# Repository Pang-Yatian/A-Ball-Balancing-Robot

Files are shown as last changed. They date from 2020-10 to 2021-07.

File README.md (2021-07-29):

# A-Ball-Balancing-Robot
## Brief introduction
A ball balancing robot is a kind of dynamical stable robot, which is designed to balance on a ball by itself, while the ball can move in any direction under the control of the robot. Actuation is realized by using DC motors to drive three omnidirectional wheels rotating, making the robot body reach its equilibrium point. An inertial measurement unit is used to detect the change in attitude angles. Based on kinematic analysis, Proportional-Integral-Derivative controllers are implemented to stabilize and control the robot.

video:  https://youtu.be/On0e1YCgcag

https://www.bilibili.com/video/BV1TJ411x7tR?p=3

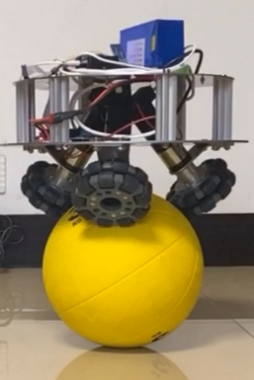
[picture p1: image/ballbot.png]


## Run
The code needs Keil uvison5 IDE to open.

--->dynamical control code\USER\Minibalance.uvprojx

## Hardware composition

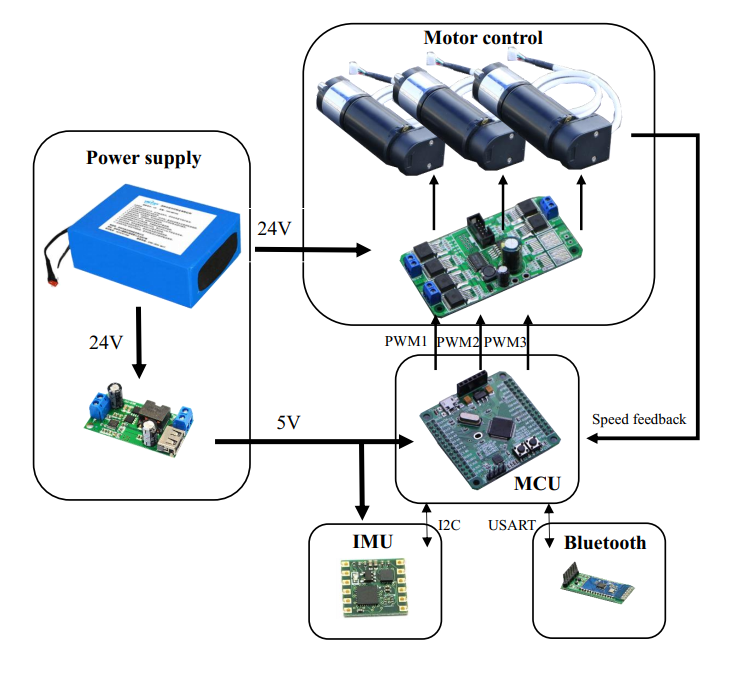
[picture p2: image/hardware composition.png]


## Hardware list

MCU:STM32F103 module

DC motor: MD36NP51 with photoelectric encoder (24V)

Motor driver: BTN7971 module

Omniwheel: diameter 100mm

Battery: 5AH 24V 5000mah

Ball: v1-v2 standard football, final version 3kg medicine ball (225mm)

IMU: MPU-6050 module

## Performance 

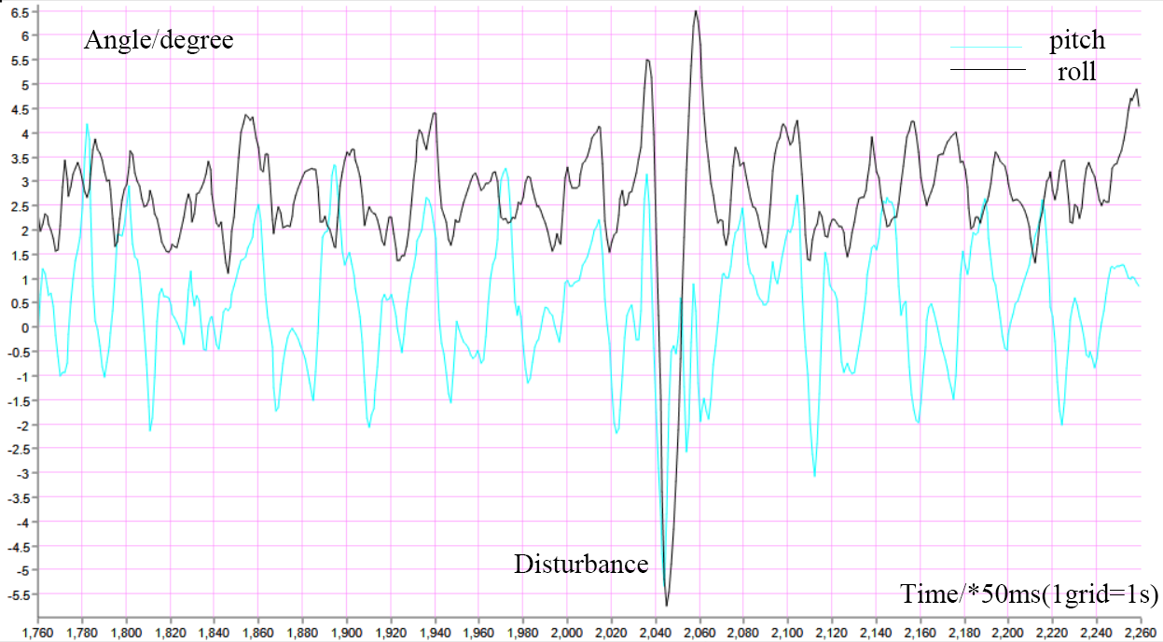
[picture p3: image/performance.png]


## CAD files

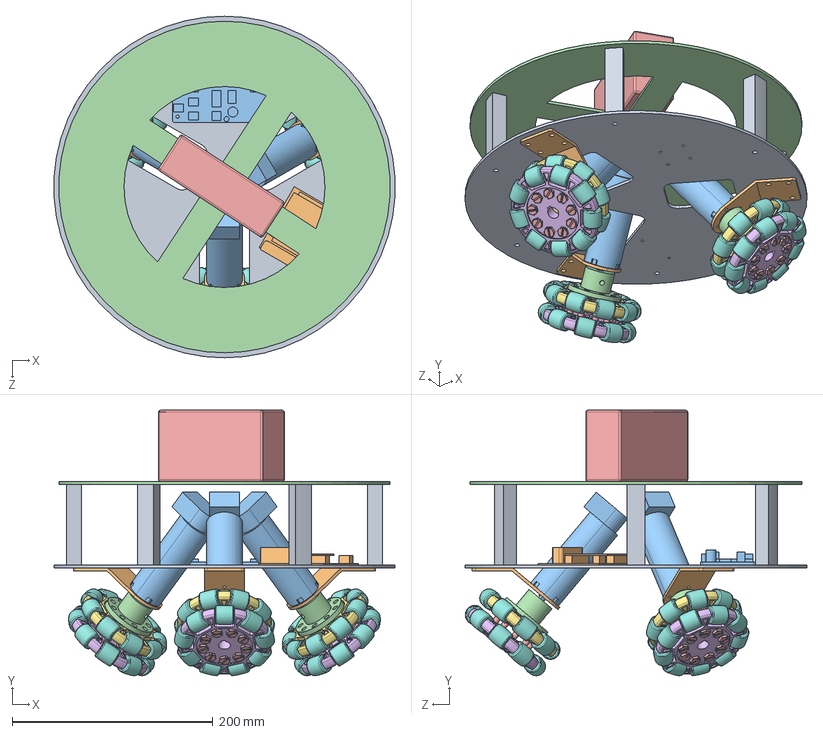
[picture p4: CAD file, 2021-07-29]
Mechanic/ballbot 50度.SLDASM
339.4 x 264.3 x 340.0 mm
底盘
电机支架 x 3
电机.stp x 3
lianzhouqi x 3
hex bolts with slot on head grade ab gb x 27
omnidirectionalwheels x 3
omnidirectionalwheels2 x 3
wheel x 54
支柱 x 6
stm32f103rc
BTN7971
板1
battery

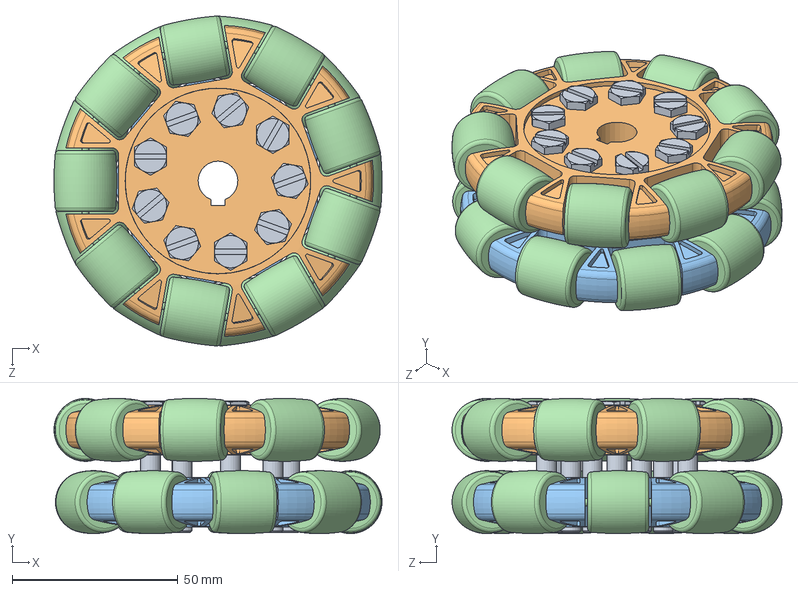
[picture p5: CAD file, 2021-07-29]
Mechanic/parts/omniwheel.SLDASM
99.0 x 40.8 x 99.6 mm
hex bolts with slot on head grade ab gb x 9
omnidirectionalwheels
omnidirectionalwheels2
wheel x 18

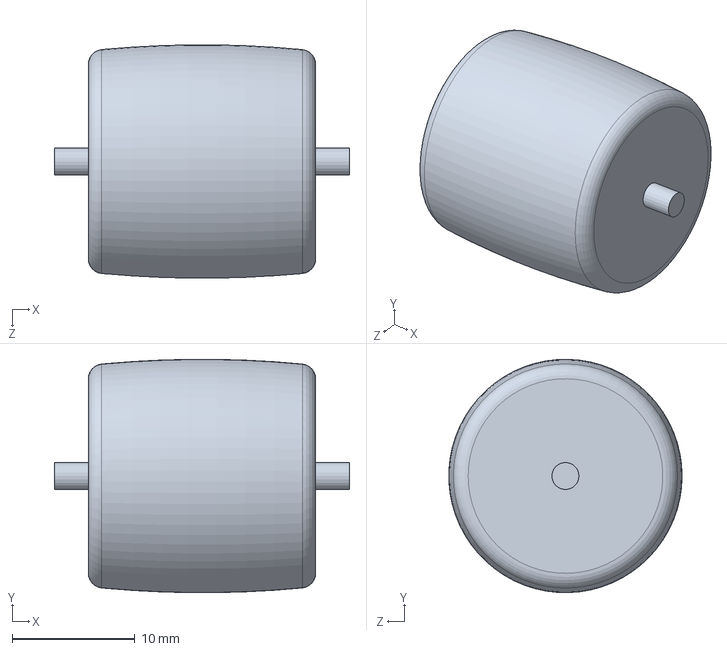
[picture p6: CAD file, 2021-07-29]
Mechanic/parts/part/wheel.SLDPRT
24.0 x 19.0 x 19.0 mm

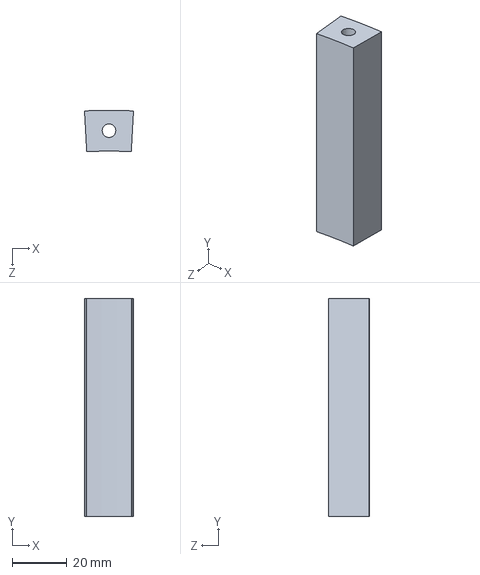
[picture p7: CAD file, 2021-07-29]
Mechanic/parts/支柱.SLDPRT
18.0 x 80.0 x 15.2 mm

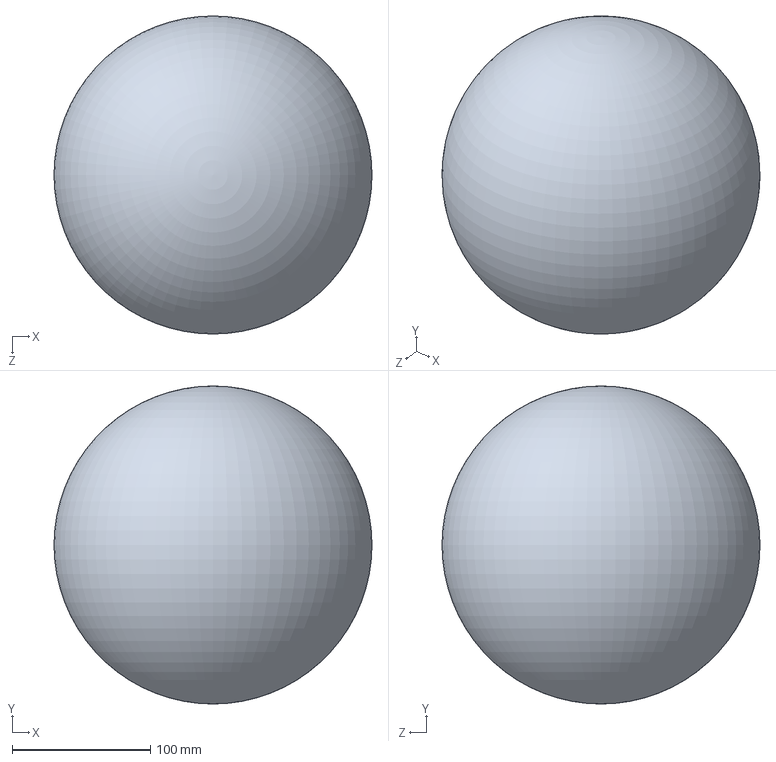
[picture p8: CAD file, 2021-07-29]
Mechanic/parts/ball.SLDPRT
230.0 x 230.0 x 230.0 mm

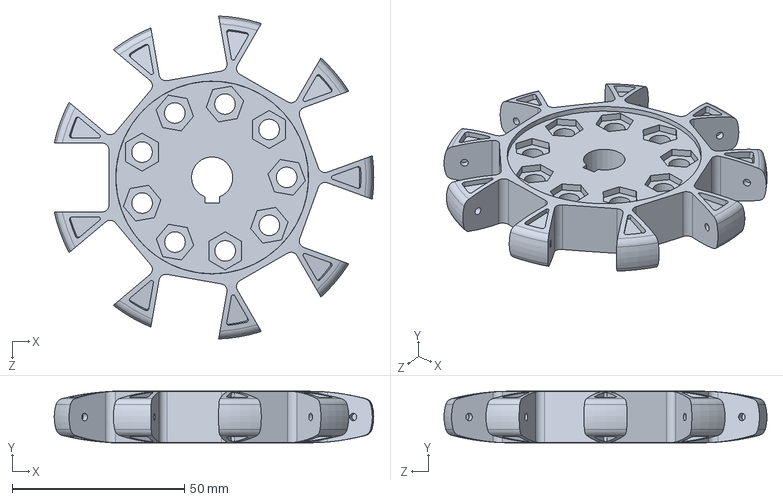
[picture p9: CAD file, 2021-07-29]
Mechanic/parts/part/omnidirectionalwheels.SLDPRT
92.9 x 15.0 x 93.9 mm

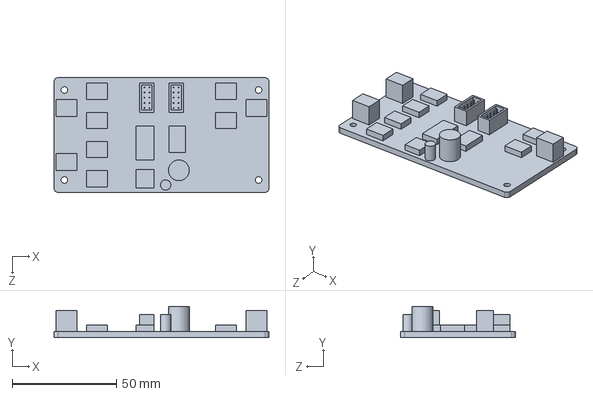
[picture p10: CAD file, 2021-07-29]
Mechanic/parts/BTN7971.SLDPRT
103.2 x 15.0 x 55.2 mm

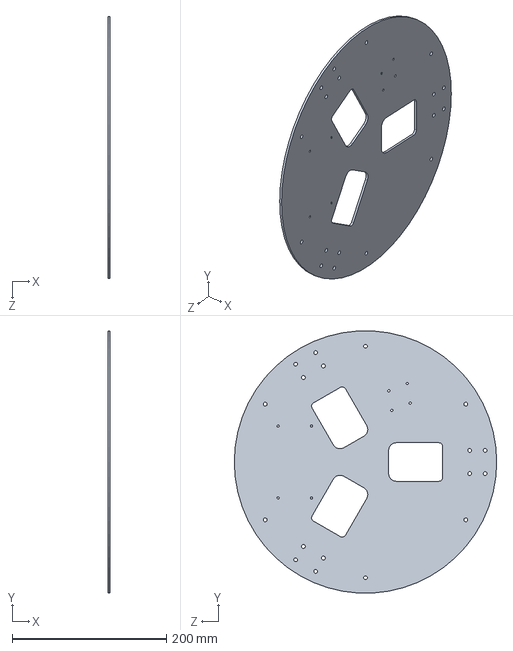
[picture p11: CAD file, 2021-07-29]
Mechanic/parts/底盘.SLDPRT
3.00 x 339.4 x 340.0 mm

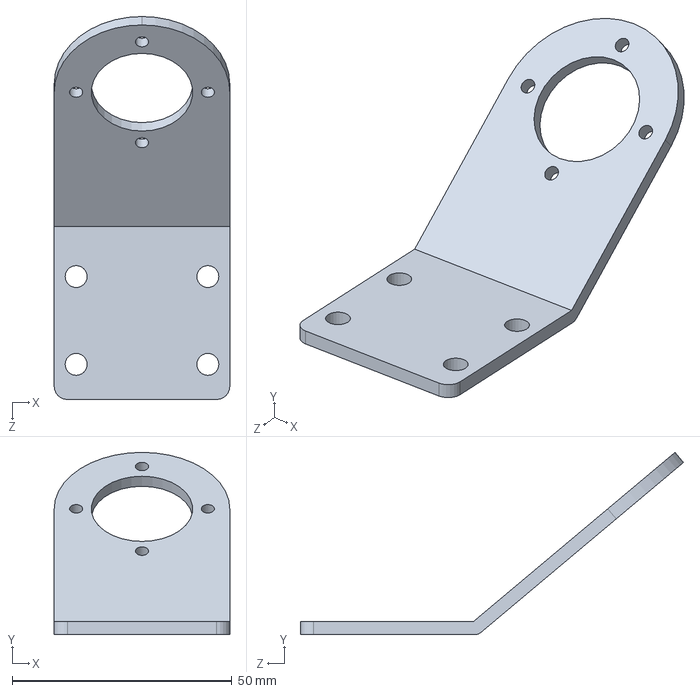
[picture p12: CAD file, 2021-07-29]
Mechanic/parts/电机支架.SLDPRT
40.0 x 41.5 x 87.2 mm

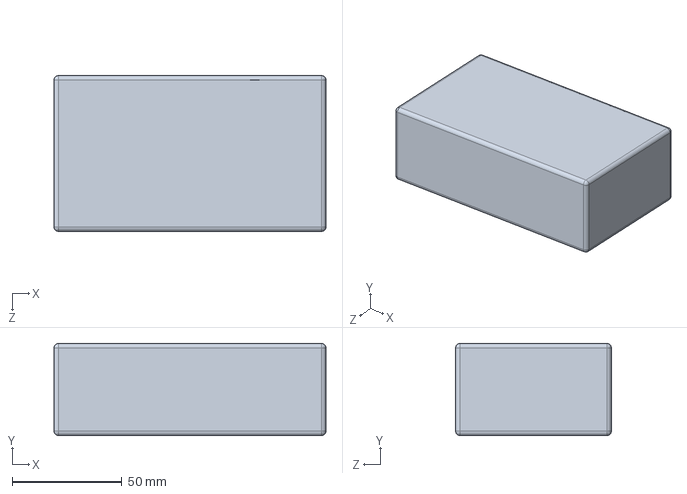
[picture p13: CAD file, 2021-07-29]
Mechanic/parts/battery.SLDPRT
124.0 x 42.0 x 71.0 mm

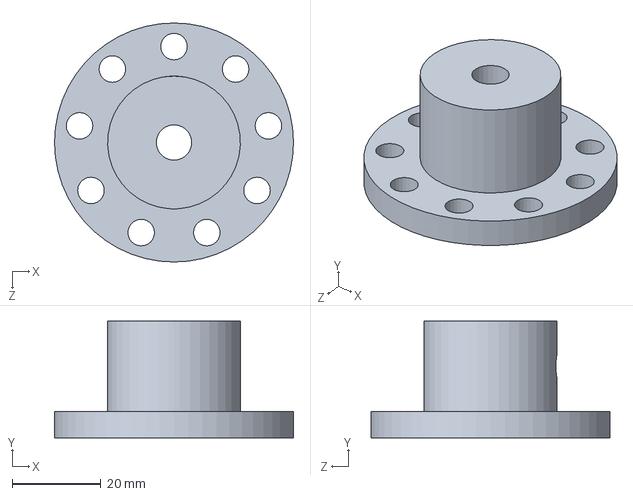
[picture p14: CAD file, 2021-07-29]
Mechanic/parts/lianzhouqi.SLDPRT
54.0 x 26.4 x 54.0 mm

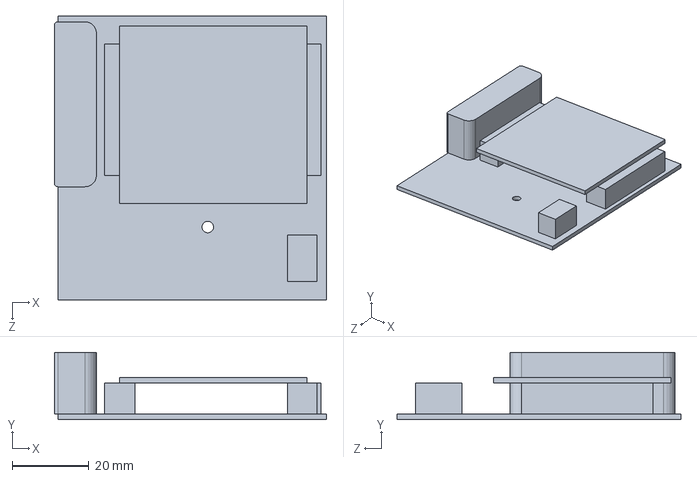
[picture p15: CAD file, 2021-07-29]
Mechanic/parts/stm32f103rc.SLDPRT
71.0 x 17.5 x 74.0 mm

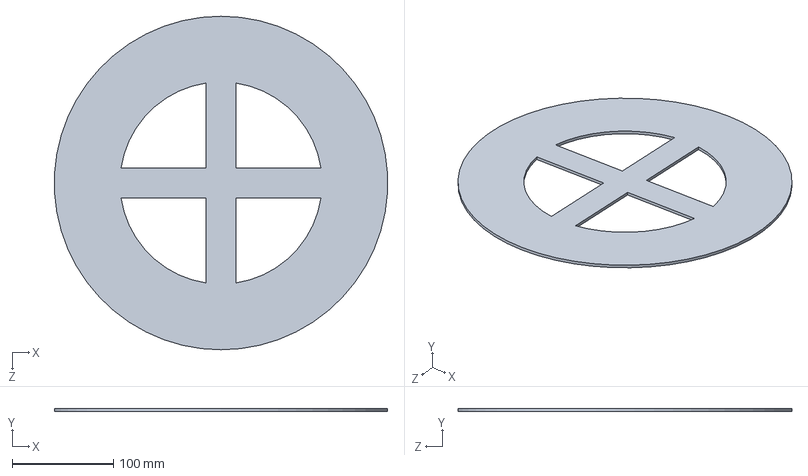
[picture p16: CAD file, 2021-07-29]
Mechanic/parts/板1.SLDPRT
329.4 x 3.00 x 330.0 mm

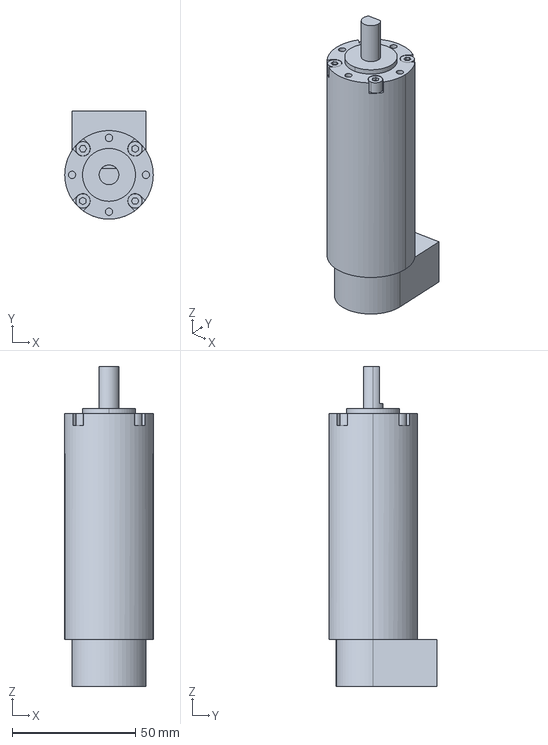
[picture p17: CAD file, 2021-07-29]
Mechanic/parts/电机.stp
36.0 x 44.0 x 130.0 mm

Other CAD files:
Mechanic/parts/part/omnidirectionalwheels2.SLDPRT

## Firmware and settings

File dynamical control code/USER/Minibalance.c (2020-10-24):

#include "sys.h"
  /**************************************************************************
作者：Pang Yatian
*
**************************************************************************/ 
u8 Flag_Stop=1,Flag_Show,Flag_Zero;      //停止标志位和 显示标志位 默认停止 显示打开
int Encoder_A,Encoder_B,Encoder_C;          //编码器的脉冲计数
u8 Flag_Qian,Flag_Hou,Flag_Left,Flag_Right,Turn_Left,Turn_Right;                  
long int Motor_A,Motor_B,Motor_C;        //电机PWM变量
long int Target_A,Target_B,Target_C;     //电机目标值
float Encoder_X,Encoder_Y,Encoder_Z,Position_X,Position_Y;;
int Voltage;                             //电池电压采样相关的变量                       
u8 delay_50,delay_flag,sudu=1;                          //延时相关变量
u8 Turn_Flag,PID_Send;  //CAN和串口控制相关变量
float Angle_Balance_X,Angle_Balance_Y,Angle_Balance_Z,Gyro_Balance_X,Gyro_Balance_Z,Gyro_Balance_Y,Move_X,Move_Y,Move_Z;   //三轴角度和XYZ轴目标速度
float	Balance_Kp=255,Balance_Kd=120,Balance_Kp1=265,Balance_Kd1=120,Velocity_Kp=78,Velocity_Ki=50,Velocity_Kp1=123,Velocity_Ki1=60,Turn_Kp=25,Turn_Kd=87;  //控制PID参数 151 88
int Angle_Zero_X, Angle_Zero_Y,Angle_Bias_X, Angle_Bias_Y;
int main(void)
{ 
	Stm32_Clock_Init(9);            //=====系统时钟设置
	delay_init(72);                 //=====延时初始化
	JTAG_Set(JTAG_SWD_DISABLE);     //=====关闭JTAG接口
	JTAG_Set(SWD_ENABLE);           //=====打开SWD接口 可以利用主板的SWD接口调试
	LED_Init();                     //=====初始化与 LED 连接的硬件接口
	KEY_Init();                     //=====按键初始化
	OLED_Init();                    //=====OLED初始化
	uart_init(72,128000);           //=====串口1初始化
	uart2_init(36,9600);            //=====串口2初始化
 // uart3_init(36,115200);          //=====串口3初始化 
	Encoder_Init_TIM2();            //=====编码器接口
	Encoder_Init_TIM3();            //=====编码器接口
	Encoder_Init_TIM4();            //=====初始化编码器C
	Encoder_Init_TIM5();            //=====初始化编码器D
	Adc_Init();                     //=====adc初始化
	IIC_Init();                     //=====IIC初始化
  MPU6050_initialize();           //=====MPU6050初始化	
  DMP_Init();                     //=====初始化DMP     
	MiniBalance_PWM_Init(7199,0);   //=====初始化PWM 10KHZ，用于驱动电机
  EXTI_Init();                    //=====MPU6050 5ms定时中断初始化
	while(1)
		{		
	    if(Flag_Show==0)           //使用MiniBalance APP和OLED显示屏
			{
				APP_Show();	              
				oled_show();             //===显示屏打开
	    }
    	else                       //使用MiniBalance上位机 上位机使用的时候需要严格的时序，故此时关闭app监控部分和OLED显示屏
  		{
				DataScope();              //开启MiniBalance上位机
			}
			delay_flag=1;	
			delay_50=0;
			while(delay_flag);	       //通过MPU6050的INT中断实现的50ms精准延时				
		} 
}

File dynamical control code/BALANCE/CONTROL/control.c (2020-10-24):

#include "control.h"	
#include "filter.h"	
  /**************************************************************************
作者：Pang Yatian
*
**************************************************************************/

u8 Flag_Target,Flag_Target2,Flag_Change;                             //相关标志位
u8 temp1;                                               //临时变量
float Voltage_Count,Voltage_All; 											 //电压采样相关变量
int Balance_Pwm_X,Velocity_Pwm_X,Balance_Pwm_Y,Velocity_Pwm_Y,Balance_Pwm_Z;
#define X_PARAMETER          (0.5f)               
#define Y_PARAMETER           (sqrt(3)/2.f)      
#define L_PARAMETER            (1.0f)    
/**************************************************************************
函数功能：小车运动数学模型
入口参数：X Y Z 三轴速度或者位置
返回  值：无
**************************************************************************/
void Kinematic_Analysis(float Vx,float Vy,float Vz)
{
	      Target_A   = -Vx + L_PARAMETER*Vz;
        Target_B   = X_PARAMETER*Vx - Y_PARAMETER*Vy + L_PARAMETER*Vz;
	      Target_C   = X_PARAMETER*Vx + Y_PARAMETER*Vy + L_PARAMETER*Vz;
}
/**************************************************************************
函数功能：小车运动 正运动学分析 注：实际注释掉的是理想的运动学分析，实际使用放大了3倍，对计算结果没影响，主要是避免舍去误差
入口参数：A B C三个电机的速度
返回  值：无
**************************************************************************/
void Encoder_Analysis(float Va,float Vb,float Vc)
{
		Encoder_X=Va*2-Vb-Vc;
		Encoder_Y=(Vc-Vb)*sqrt(3);
		Encoder_Z=Va+Vb+Vc;
}
/**************************************************************************
函数功能：所有的控制代码都在这里面
         5ms定时中断由MPU6050的INT引脚触发
         严格保证采样和数据处理的时间同步				 
**************************************************************************/
int EXTI15_10_IRQHandler(void) 
{    
	 if(INT==0)		
	{     
		  EXTI->PR=1<<15;                                                      //清除LINE5上的中断标志位  	        		
		  if(delay_flag==1)
			 {
				 if(++delay_50==10)	 delay_50=0,delay_flag=0;                     //给主函数提供50ms的精准延时
			 }             
       Flag_Target2=!Flag_Target2;  //角度采集分频标志位
			 if(Flag_Target2==1)
			 {
			 	Read_DMP();  //采集角度
				Key();//扫描按键变化	
		    if(Flag_Show==0)Led_Flash(100);  //===LED闪烁;常规模式 1s改变一次指示灯的状态	
				else Led_Flash(0); //上位机模式常亮
				Voltage_All+=Get_battery_volt();   //多次采样累积采集电池电压
			  if(++Voltage_Count==100) Voltage=Voltage_All/100,Voltage_All=0,Voltage_Count=0;//求平均值 获取电池电压	 
         return 0;				 
			 }
			Encoder_A=-Read_Encoder(2);  //===读取编码器的值 为了保证M法测速的时间基准，首先读取编码器数据
			Encoder_B=-Read_Encoder(3);  //===读取编码器的值  
			Encoder_C=-Read_Encoder(4);  //===读取编码器的值+=Encoder_A/20;
				
			Angle_Bias_X =Angle_Balance_X-Angle_Zero_X;		//获取Y方向的偏差
		  Angle_Bias_Y =Angle_Balance_Y-Angle_Zero_Y;		//获取Y方向的偏差
			Encoder_Analysis(Encoder_A,Encoder_B,Encoder_C);//对编码器的数据进行正运动学分析
			  Position_X+=Encoder_X;
			  Position_Y+=Encoder_Y;
	  	Read_DMP();   //读取角度 
			Balance_Pwm_X= balance_X(Angle_Bias_X,Gyro_Balance_X);//X方向的倾角控制
			Balance_Pwm_Y= balance_Y(Angle_Bias_Y,Gyro_Balance_Y);	//Y方向的倾角控制
			Balance_Pwm_Z= -balance_Z(Encoder_Z,Gyro_Balance_Z);		//Z方向倾角控制
       if(++Flag_Target==4)			//速度控制分频标志位 
			  {
				Velocity_Pwm_X=velocity_X(Encoder_X);  //X方向的速度控制  
				Velocity_Pwm_Y=velocity_Y(Encoder_Y);  //Y方向的速度控制
					Flag_Target=0;				 
			  }
			  Move_X =Balance_Pwm_X+Velocity_Pwm_X;   //===X方向控制量累加					
			  Move_Y =Balance_Pwm_Y+Velocity_Pwm_Y;   //===Y方向控制量累加					
			  Move_Z=Balance_Pwm_Z;				 //===Z方向控制量累加	
 				Kinematic_Analysis(Move_X,Move_Y,Move_Z);//逆运动学分析，得到A B C电机控制量
			  Xianfu_Pwm(3000);//===PWM频率限幅
				Motor_A=Target_A;//直接调节PWM占空比 
				Motor_B=Target_B;//直接调节PWM占空比
				Motor_C=Target_C;//直接调节PWM占空比
		    if(Turn_Off(Voltage)==0)  //===如果电池电压不存在异常
				Set_Pwm(Motor_A,Motor_B,Motor_C);    //赋值给PWM寄存器	
					 if(Flag_Zero)  // //这是人为更新零点值
				 {
						 Angle_Zero_Y=Angle_Balance_Y;//Y方向角度更新
						 Angle_Zero_X=Angle_Balance_X;//X方向角度更新
						 Flag_Zero=0;//清零过程仅执行一次 等待下一次指令
				 }		 				 
 }
	 return 0;			
} 
/**************************************************************************
函数功能：Z轴控制
入口参数：Z轴速度、Z轴角速度
返回  值：Z轴控制控制PWM
作    者：Pang Yatian
**************************************************************************/
int balance_Z(float Velocity,float Gyro)
{  
   float Bias,Target;   //偏差和目标值
	 static float Target_Velocity=600;//遥控的速度
	 int balance,turn_kd;
	 if(Turn_Left==1)Target=Target_Velocity/sudu,turn_kd=0;   //控制自转
	 else if(Turn_Right==1)Target=-Target_Velocity/sudu,turn_kd=0;
	 else Target=0,turn_kd=Turn_Kd;
	 Bias=Velocity-Target;        //===求出平衡的角度中值 和机械相关
	 balance=Turn_Kp*Bias/10+Gyro*turn_kd/100;   //===计算平衡控制的电机PWM  PD控制   kp是P系数 kd是D系数  
	 return balance;
}
/**************************************************************************
函数功能：直立PD控制Y
入口参数：角度、角速度
返回  值：直立控制PWM
作    者：Pang Yatian
**************************************************************************/
int balance_Y(float Angle,float Gyro)
{  
   float Bias;
	 int balance;
	 Bias=Angle;        //===求出平衡的角度中值 和机械相关
	 balance=Balance_Kp1*Bias+Gyro*Balance_Kd1/100;   //===计算平衡控制的电机PWM  PD控制   kp是P系数 kd是D系数 
	 return balance;
}
/**************************************************************************
函数功能：直立PD控制
入口参数：角度、角速度
返回  值：直立控制PWM
作    者：Pang Yatian
**************************************************************************/
int balance_X(float Angle,float Gyro)
{  
   float Bias;
	 int balance;
	 Bias=Angle;        //===求出平衡的角度中值 和机械相关
	 balance=Balance_Kp*Bias+Gyro*Balance_Kd/100;   //===计算平衡控制的电机PWM  PD控制   kp是P系数 kd是D系数 
	 return balance;
}

/**************************************************************************
函数功能：速度PI控制 修改前进后退速度，请修Target_Velocity
入口参数：左轮速度、右轮速度
返回  值：速度控制PWM
作    者：Pang Yatian
**************************************************************************/
int velocity_X(int velocity)
{  
    static float Velocity,Encoder_Least,Encoder,Movement;
	  static float Target_Velocity=1200;//遥控的速度
	  static float Encoder_Integral;  //积分变量
			if(1==Flag_Left)    	Movement=Target_Velocity/sudu;	           //===前进标志位置1 
		else if(1==Flag_Right)	Movement=-Target_Velocity/sudu;           //===后退标志位置1
  	else  Movement=0;
//   //=============速度PI控制器=======================//	
		Encoder_Least=velocity;          //速度采集  
		Encoder *= 0.7;		                                                //===一阶低通滤波器       
		Encoder += Encoder_Least*0.3;	                                    //===一阶低通滤波器    
		Encoder_Integral +=Encoder;                                       //===积分出位移 
		Encoder_Integral +=Movement;                                      //===接收遥控器数据，控制前进后退
		if(Encoder_Integral>550000)  	Encoder_Integral=550000;             //===积分限幅
		if(Encoder_Integral<-550000)	Encoder_Integral=-550000;              //===积分限幅	
	  Velocity=Encoder*Velocity_Kp/100+Encoder_Integral*Velocity_Ki/5000;        //===速度控制	
  	if(Flag_Stop)   Encoder_Integral=0,Encoder=0;      //===电机关闭后清除积分
	  return Velocity;
}
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

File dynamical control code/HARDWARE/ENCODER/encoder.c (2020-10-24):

#include "encoder.h"
  /**************************************************************************
作者：Pang Yatian
*
**************************************************************************/
/**************************************************************************
函数功能：把TIM2初始化为编码器接口模式
入口参数：无
返回  值：无
**************************************************************************/
void Encoder_Init_TIM2(void)
{
//	RCC->APB2ENR|=1<<0;    //开启辅助时钟
	AFIO->MAPR|=1<<8;      //01部分重映射
	RCC->APB1ENR|=1<<0;     //TIM2时钟使能
	RCC->APB2ENR|=1<<2;    //使能PORTA时钟
	RCC->APB2ENR|=1<<3;    //使能PORTB时钟
	GPIOA->CRH&=0X0FFFFFFF;//PA15
	GPIOA->CRH|=0X40000000;//浮空输入
	
	GPIOB->CRL&=0XFFFF0FFF;//PB3
	GPIOB->CRL|=0X00004000;//浮空输入
	TIM2->DIER|=1<<0;   //允许更新中断				
	TIM2->DIER|=1<<6;   //允许触发中断
	MY_NVIC_Init(1,3,TIM2_IRQn,1);
	TIM2->PSC = 0x0;//预分频器
	TIM2->ARR = ENCODER_TIM_PERIOD;//设定计数器自动重装值 
	TIM2->CR1 &=~(3<<8);// 选择时钟分频：不分频
	TIM2->CR1 &=~(3<<5);// 选择计数模式:边沿对齐模式
		
	TIM2->CCMR1 |= 1<<0; //CC1S='01' IC1FP1映射到TI1
	TIM2->CCMR1 |= 1<<8; //CC2S='01' IC2FP2映射到TI2
	TIM2->CCER &= ~(1<<1);	 //CC1P='0'	 IC1FP1不反相，IC1FP1=TI1
	TIM2->CCER &= ~(1<<5);	 //CC2P='0'	 IC2FP2不反相，IC2FP2=TI2
//	TIM2->CCMR1 |= 3<<4; //	IC1F='1000' 输入捕获1滤波器
	TIM2->SMCR |= 3<<0;	 //SMS='011' 所有的输入均在上升沿和下降沿有效
	TIM2->CR1 |= 0x01;    //CEN=1，使能定时器
}
/**************************************************************************
函数功能：把TIM3初始化为编码器接口模式
入口参数：无
返回  值：无
**************************************************************************/
void Encoder_Init_TIM3(void)
{
	RCC->APB1ENR|=1<<1;     //TIM2时钟使能
	RCC->APB2ENR|=1<<3;    //使能PORTA时钟
	GPIOA->CRL&=0X00FFFFFF;//PA6 PA7
	GPIOA->CRL|=0X44000000;//浮空输入
	TIM3->DIER|=1<<0;   //允许更新中断				
	TIM3->DIER|=1<<6;   //允许触发中断
	MY_NVIC_Init(1,3,TIM3_IRQn,1);
	TIM3->PSC = 0x0;//预分频器
	TIM3->ARR = ENCODER_TIM_PERIOD;//设定计数器自动重装值 
	TIM3->CR1 &=~(3<<8);// 选择时钟分频：不分频
	TIM3->CR1 &=~(3<<5);// 选择计数模式:边沿对齐模式
		
	TIM3->CCMR1 |= 1<<0; //CC1S='01' IC1FP1映射到TI1
	TIM3->CCMR1 |= 1<<8; //CC2S='01' IC2FP2映射到TI2
	TIM3->CCER &= ~(1<<1);	 //CC1P='0'	 IC1FP1不反相，IC1FP1=TI1
	TIM3->CCER &= ~(1<<5);	 //CC2P='0'	 IC2FP2不反相，IC2FP2=TI2
//	TIM2->CCMR1 |= 3<<4; //	IC1F='1000' 输入捕获1滤波器
	TIM3->SMCR |= 3<<0;	 //SMS='011' 所有的输入均在上升沿和下降沿有效
	TIM3->CR1 |= 0x01;    //CEN=1，使能定时器
}
/**************************************************************************
函数功能：把TIM4初始化为编码器接口模式
入口参数：无
返回  值：无
**************************************************************************/
void Encoder_Init_TIM4(void)
{
	RCC->APB1ENR|=1<<2;     //TIM4时钟使能
	RCC->APB2ENR|=1<<3;     //使能PORTB时钟
	GPIOB->CRL&=0X00FFFFFF; //PB6 PB7
	GPIOB->CRL|=0X44000000; //浮空输入
	TIM4->DIER|=1<<0;   //允许更新中断				
	TIM4->DIER|=1<<6;   //允许触发中断
	MY_NVIC_Init(1,3,TIM4_IRQn,1);
	TIM4->PSC = 0x0;//预分频器
	TIM4->ARR = ENCODER_TIM_PERIOD;//设定计数器自动重装值 
	TIM4->CR1 &=~(3<<8);// 选择时钟分频：不分频
	TIM4->CR1 &=~(3<<5);// 选择计数模式:边沿对齐模式
		
	TIM4->CCMR1 |= 1<<0; //CC1S='01' IC1FP1映射到TI1
	TIM4->CCMR1 |= 1<<8; //CC2S='01' IC2FP2映射到TI2
	TIM4->CCER &= ~(1<<1);	 //CC1P='0'	 IC1FP1不反相，IC1FP1=TI1
	TIM4->CCER &= ~(1<<5);	 //CC2P='0'	 IC2FP2不反相，IC2FP2=TI2
//	TIM4->CCMR1 |= 3<<4; //	IC1F='1000' 输入捕获1滤波器
	TIM4->SMCR |= 3<<0;	 //SMS='011' 所有的输入均在上升沿和下降沿有效
	TIM4->CR1 |= 0x01;    //CEN=1，使能定时器
}
/**************************************************************************
函数功能：把TIM5初始化为编码器接口模式
入口参数：无
返回  值：无
**************************************************************************/
void Encoder_Init_TIM5(void)
{
	RCC->APB1ENR|=1<<3;     //TIM5时钟使能
	RCC->APB2ENR|=1<<2;    //使能PORTA时钟
	GPIOA->CRL&=0XFFFFFF00;//PA0 PA1
	GPIOA->CRL|=0X00000044;//浮空输入
	TIM2->DIER|=1<<0;   //允许更新中断				
	TIM2->DIER|=1<<6;   //允许触发中断
	MY_NVIC_Init(1,3,TIM5_IRQn,1);
	TIM5->PSC = 0x0;//预分频器
	TIM5->ARR = ENCODER_TIM_PERIOD;//设定计数器自动重装值 
	TIM5->CR1 &=~(3<<8);// 选择时钟分频：不分频
	TIM5->CR1 &=~(3<<5);// 选择计数模式:边沿对齐模式
		
	TIM5->CCMR1 |= 1<<0; //CC1S='01' IC1FP1映射到TI1
	TIM5->CCMR1 |= 1<<8; //CC2S='01' IC2FP2映射到TI2
	TIM5->CCER &= ~(1<<1);	 //CC1P='0'	 IC1FP1不反相，IC1FP1=TI1
	TIM5->CCER &= ~(1<<5);	 //CC2P='0'	 IC2FP2不反相，IC2FP2=TI2
//	TIM2->CCMR1 |= 3<<4; //	IC1F='1000' 输入捕获1滤波器
	TIM5->SMCR |= 3<<0;	 //SMS='011' 所有的输入均在上升沿和下降沿有效
	TIM5->CR1 |= 0x01;    //CEN=1，使能定时器
}
/**************************************************************************
函数功能：单位时间读取编码器计数
入口参数：定时器
返回  值：速度值
**************************************************************************/
int Read_Encoder(u8 TIMX)
{
    int Encoder_TIM;    
   switch(TIMX)
	 {
	   case 2:  Encoder_TIM= (short)TIM2 -> CNT;   TIM2 -> CNT=0; break;
		 case 3:  Encoder_TIM= (short)TIM3 -> CNT;   TIM3 -> CNT=0; break;
		 case 4:  Encoder_TIM= (short)TIM4 -> CNT;   TIM4 -> CNT=0;  break;	
		 case 5:  Encoder_TIM= (short)TIM5 -> CNT;   TIM5 -> CNT=0;  break;	
		 default:  Encoder_TIM=0;
	 }
		return Encoder_TIM;
}
/**************************************************************************
函数功能：TIM2中断服务函数
入口参数：无
返回  值：无
**************************************************************************/
void TIM2_IRQHandler(void)
{ 		    		  			    
	if(TIM2->SR&0X0001)//溢出中断
	{    				   				     	    	
	}				   
	TIM2->SR&=~(1<<0);//清除中断标志位 	    
}

/**************************************************************************
函数功能：TIM3中断服务函数
入口参数：无
返回  值：无
**************************************************************************/
void TIM3_IRQHandler(void)
{ 		    		  			    
	if(TIM3->SR&0X0001)//溢出中断
	{    				   				     	    	
	}				   
	TIM3->SR&=~(1<<0);//清除中断标志位 	    
}
/**************************************************************************
函数功能：TIM4中断服务函数
入口参数：无
返回  值：无
**************************************************************************/
void TIM4_IRQHandler(void)
{ 		    		  			    
	if(TIM4->SR&0X0001)//溢出中断
	{    				   				     	    	
	}				   
	TIM4->SR&=~(1<<0);//清除中断标志位 	    
}

/**************************************************************************
函数功能：TIM4中断服务函数
入口参数：无
返回  值：无
**************************************************************************/
void TIM5_IRQHandler(void)
{ 		    		  			    
	if(TIM5->SR&0X0001)//溢出中断
	{    				   				     	    	
	}				   
	TIM5->SR&=~(1<<0);//清除中断标志位 	    
}
